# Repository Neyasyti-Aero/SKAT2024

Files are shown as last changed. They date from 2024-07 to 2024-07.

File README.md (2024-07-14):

# SKAT2024
Репозиторий для выполнения требований к подготовке производственного отчета команды **НЕЯСЫТИ АЭРО**, принявшей участие в СКАТ 2024

# Файлы
Схемы плат представлены в формате *SchDoc (Altium Designer)*. Для их просмотра можно использовать online-инструмент [Altium Viewer](https://www.altium.com/viewer/). Структурная схема (в составе схемы бортового оборудования) и фотографии изделия в сборе представлены в полном тексте производственного отчета команды **НЕЯСЫТИ АЭРО**.

# Полетный контроллер Стриж
Полетный контроллер «Стриж» - изделие собственной разработки, на основе микросхемы `К1921ВК01Т2` (ядро `ARM Cortex-M4`), которую можно считать достаточно близким аналогом `STM32F427ZGT6`. Максимальная тактовая частота − 200 МГц.

Компоновка изделия: 3 печатные платы в пластмассовом корпусе (плата питания нижняя, плата контроллера верхняя, плата ПР1803Н − убраны в пластмассовый корпус, изготовленный методом 3D-печати). Плата питания (нижняя плата) имеет размер 53x55 мм, средняя и верхняя − размером 53x45 мм, их коммутация осуществляется посредством межплатных разъемов, расположенных по краям (по длине) изделия. Электропитание на плату подается от литий-полимерной аккумуляторной батареи через силовой разъем XT60-M, расположенный на нижней плате. Питание подводится к выводу входного напряжения VIN DC-DC преобразователя `MP1584EN`, его выходное напряжение составляет 5В. Это напряжение подаётся на вход расположенного на верхней плате линейного регулятора напряжения `КФ1158Н`, который питает микроконтроллер `К1921ВК01Т2`, инерциальный модуль, компас и внешние подключаемые устройства (выходное напряжение стабилизатора 3,3 В). Помимо силового разъёма XT60-M, питание на микроконтроллер, датчики и внешние устройства может быть подано при подключении полетного контроллера к компьютеру посредством разъема USB TYPE-C-31-M-12, или же при подключении программатора-отладчика. Для подключения к полетному контроллеру сервоприводов на нижней плате предусмотрены 13 выходов питания и ШИМ-сигнала управления. ESC подключаются к полетному контроллеру по CAN-шине. Питание на сервоприводы может быть подано только при подключении к полетному контроллеру аккумуляторной батареи. Для питания сервоприводов на нижней плате устанавливается отдельный DC-DC преобразователь `MP1584EN`, выходное напряжение Vout = 5 В, максимальный ток – 3 А.

Три платы (верхняя, ПР1803Н, и нижняя) полетного контроллера STRIZH соеденяются между собой посредством двухрядных межплатных разъемов с шагом 1.27 мм.

## Верхняя плата
Плата, содержащая микроконтроллер и датчики с системой их термостабилизации. Для питания датчиков (3.3 В) предназначен отдельный линейный регулятор напряжения `КФ1158Н`, на вход которого подается напряжение 5 В с нижней платы.

На плате один разъем типа picoblade для подключения отладчика-программатора (SWD), и одно USB Type-C гнездо для подключения к наземной станции (ПК с конфигуратором). Гнездо Type-C также может быть использовано для программирования (для входа в DFU-режим необходимо нажать кнопку BOOT на нижней плате при подаче питания).

Среди интегральных микросхем на плате, помимо датчиков и микроконтроллера, внешняя Nor-flash память (подключение к МК - SPI), а также трансивер CAN-интерфейса.

Для световой индикации используются 3 светодиода.

Список датчиков:
- `QMC5883L` (компас)
- `BMM150` (компас)
- `BMI055` (IMU)
- `BMI270` (IMU)
- `QMI8658` (IMU)
- `BMP388` (барометр)
- `BMP280` (барометр)

Их характеристики приводятся в тексте производственного отчета.

IMU-датчики полетного контроллера STRIZH помещены в корпус малых размеров (термостат, на схеме не показан), внутри которого за счет обогрева резисторами поддерживается постоянная температура (обратная связь – резистивные делители напряжения с термисторами в нижнем плече, термисторы расположены вблизи датчиков). Таким образом, система термостатирования представляет из себя замкнутую систему автоматического регулирования, в качестве устройства управления выступает микроконтроллер: программно реализован ПИ-регулятор температуры внутри термостата. Повышение отказоустойчивости системы в целом достигается за счет двойного-тройного резервирования всех критически важных составляющих её элементов. Отказ датчика обнаруживается микроконтроллером при отсутствии от соответствующего датчика (в течение заданного тайм-аута) ответа на управляющий байт во время операции чтения.

## ПР1803Н
Плата с навигационно-связным модулем `ПР1803Н`. Питание (4.2 В) подается с нижней платы. Подключен к микроконтроллеру через межплатный разъем (UART)

`ПР1803Н` - навигационно-связной модуль, в разработанном полетном контроллере Стриж используется для передачи телеметрии через сотовую связь, а также для мультисистемного (GPS, ГЛОНАСС, BeiDou, Galileo) позиционирования. Рабочий частотный диапазон: B1 (LTE FDD). Частота передачи: от 1920 до 1980 МГц. Частота приема: от 2110 до 2170 МГц.

## Нижняя плата
Плата используется для подачи питания на верхнюю плату (5 В), плату с ПР1803Н (4.2 В), сервоприводы (5 В). Для этого используются три DC/DC преобразователя `MP1584EN`, на входы которых подается напряжение АКБ.

Имеет разъемы (типа picoblade) USART, I2C, SPI, CAN для подключения внешних устройств, гнездо USB Type-C для питания Orange Pi. Помимо того на плате два силовых разъема XT60 для подключения АКБ (от 2S до 6S) и ESC, 13 ШИМ-выходов сервоприводов/моторов.

На плате микросхема OSD-генератора `AT7456`, который подключен к микроконтроллеру через межплатный разъем (SPI). Для подключения камеры и VTX на плате 2 разъема типа picoblade. Напряжение питания камеры - 5 В, напряжение питания VTX соответствует напряжению АКБ.

На плате 2 светодиода, 1 кнопка (BOOT, для программирования в режиме DFU).

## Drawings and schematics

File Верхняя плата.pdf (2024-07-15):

X1

| | U1

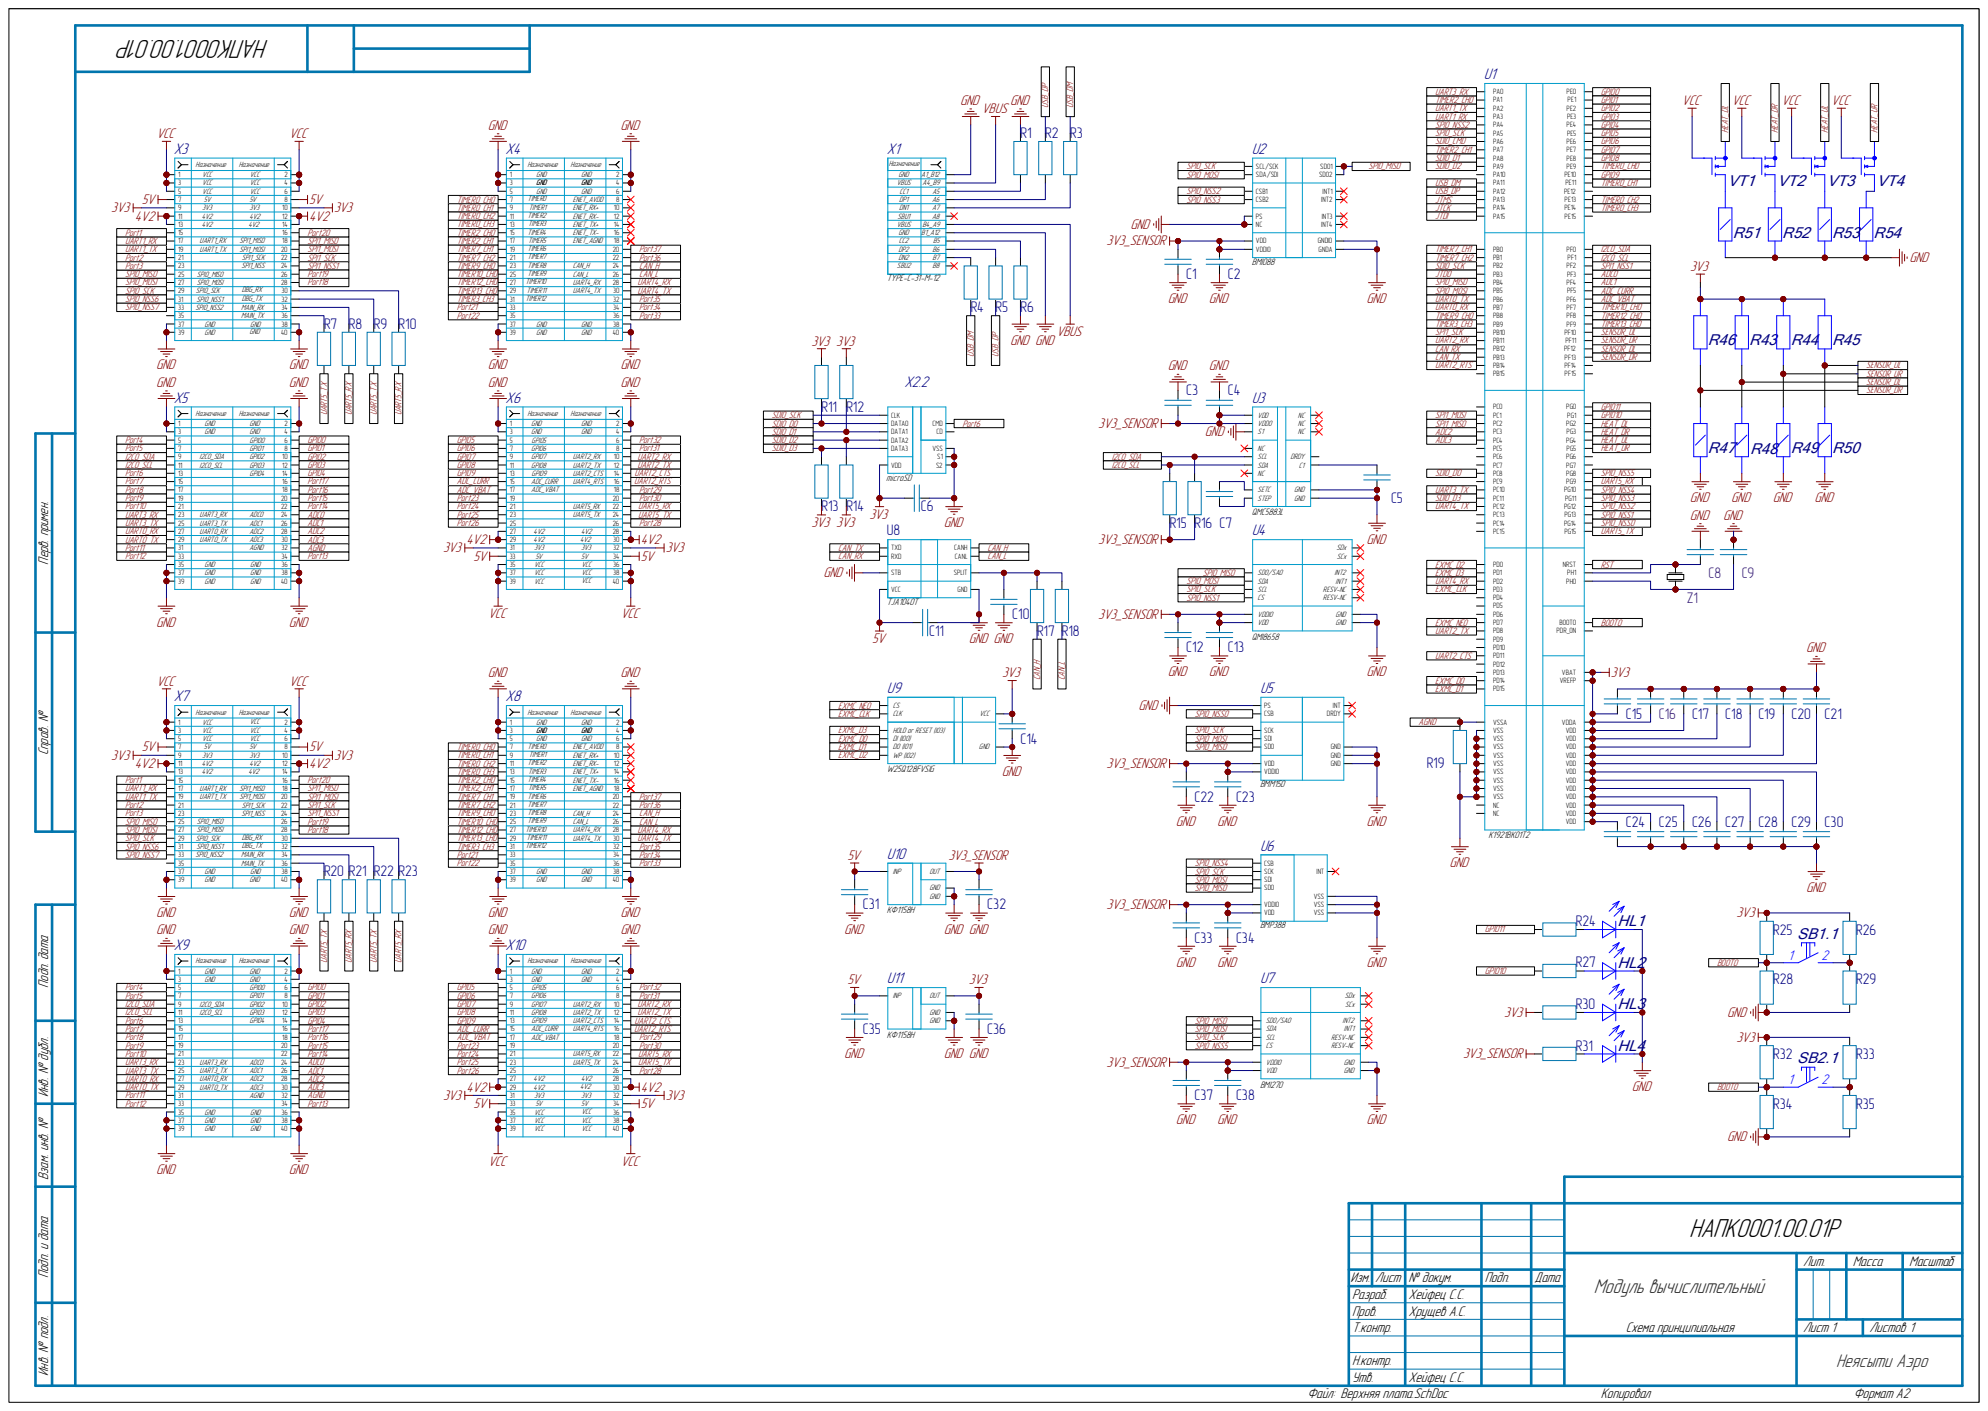
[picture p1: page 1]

GND GND
GND

НАПК0001.00.01Р

Модуль вычислительный Схема принципиальная | Лит. | Масса | Масштаб

Изм. Лист № докум. | | Подп. | Дата
Разраб. | Хейфец С.С.

Т.контр. | Лист 1 1 | Листов

Н.контр.
Утв. | Хейфец С.С.

Неясыти Аэро

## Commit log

2024-07-14 Загрузить схемы
    [Верхняя плата.SchDoc, Нижняя плата.SchDoc, ПР1803Н.SchDoc]
2024-07-14 Добавить README.md
2024-07-14 Обновить README.md
2024-07-15 Обновить Верхняя плата.pdf
